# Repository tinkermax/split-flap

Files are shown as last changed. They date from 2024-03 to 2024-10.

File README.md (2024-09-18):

# Mechanical split-flap display
You can find full details and discussion on my [blog](https://tinkerwithtech.net/split-flap-display-brings-back-memories).

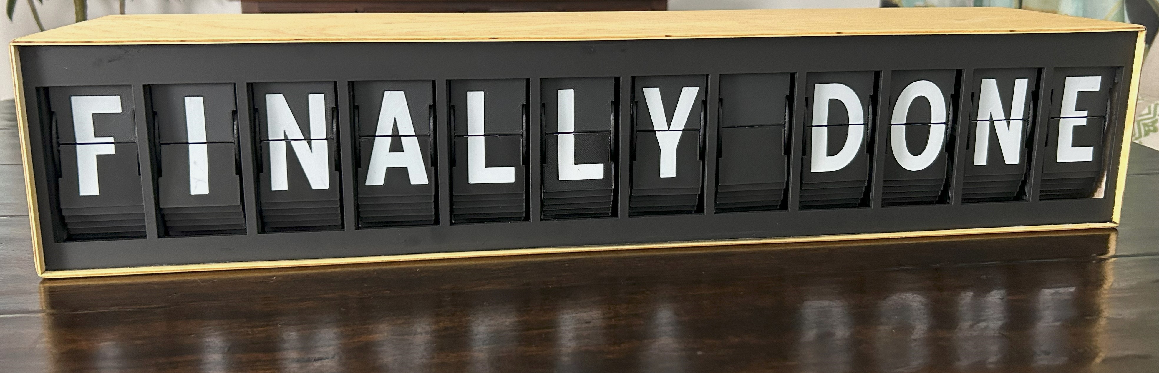
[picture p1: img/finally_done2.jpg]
Finished Split-Flap Project

<br/>

This is an alternate electronics and firmware for David Kingsman's [Split-Flap Display](https://www.printables.com/model/69464-split-flap-display).

### Advantages
* Only one microprocessor is needed to drive a 12 character display, instead of the 13 microprocessors that would be required in the original design.
* Off-the-shelf ribbon cables are used between PCBs to reduce custom wiring.
* All components are through-hole mounted (i.e. no SMD).
* Overall, this should reduce assembly time and effort.

### Disadvantages
* PCBs are not mounted to the back of the display units but have their own mounting brackets. This approach is best suited for use in your own enclosure.
* A display of greater than 12 characters would require an additional controller board i.e. may not be as seamless as the original.
<br/><br/>

## Settings
### Turn on interactions and debugging over the USB serial port in [debug.h](include/debug.h):
DEBUG 1
<br/>
### Specify the number of Units (characters) in your display (4 -12) in [system.h](include/system.h):
unitCount 12
### Specify the network name of the display (useful if you have more than one display) in [system.h](include/system.h):
NETWORKNAME "splitflap"
<br/>
### Customise for each unit for your build. (Units are numbered left to right 0 - 11) in [unit.h](include/unit.h):
calOffsetUnit : an array of the offsets to move from hall sensor trigger to blank flap<br/>
FlapStep : an array containing the number of steps per stepper revolution (then divided by 45 flaps)
<br/>
### Password and localisation settings in [config.h](include/config.h):
WIFI_SSID "mySSID"<br/>
WIFI_PWD "myPassword"

MY_NTP_SERVER "au.pool.ntp.org" // Set the best fitting NTP server (pool) for your location<br/>
MY_TZ "AEST-10AEDT,M10.1.0,M4.1.0/3" // Set your time zone from https://github.com/nayarsystems/posix_tz_db/blob/master/zones.csv

WORDNIKAPIKEY "" // Get your private key from https://developer.wordnik.com/<br/>
MINWORDLEN 9 // Specify minimum word length to fetch from Wordnik<br/>
WORDUPDATESPERHOUR 1 // Set number of word updates from https://wordnik.com per hour. 0 will disable, else use an integer that results in an exact number of minutes btw updates i.e. 1,2,3,4,5,6,10,12,15,20,30 or 60
<br/><br/>
## Libraries
This project makes extensive use of two libraries:
* [FastAccelStepper](https://github.com/gin66/FastAccelStepper) by J.Kiemes
* [arduino-mcp23017](https://github.com/blemasle/arduino-mcp23017) by Bertrand Lemasle
<br/><br/>

## Connecting to the display
### There is a very basic web page served at http://splitflap.local/ to allow you to either enter text to display or fetch a random word from Wordnik 

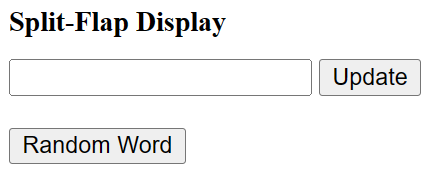
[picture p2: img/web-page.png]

<br/>

### There is also an API endpoint that you can POST to at http://splitflap.local/display, using a JSON payload in the body:

```json
{
    displaytext: "Display Text"
}
```

For example, you could use the request node within node-red:

<br/>
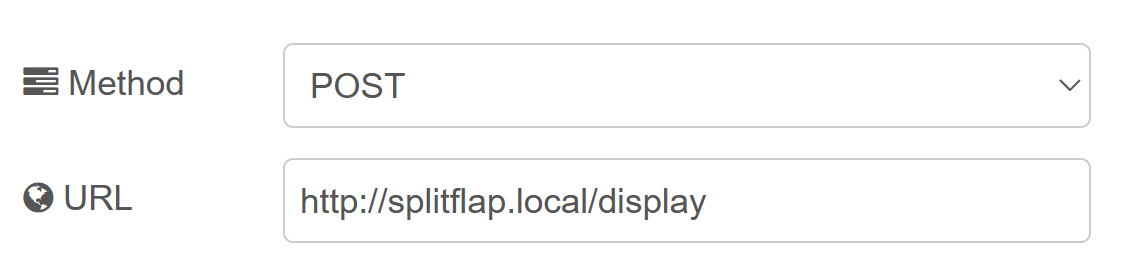
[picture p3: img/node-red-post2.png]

<br/><br/>

## PCBs
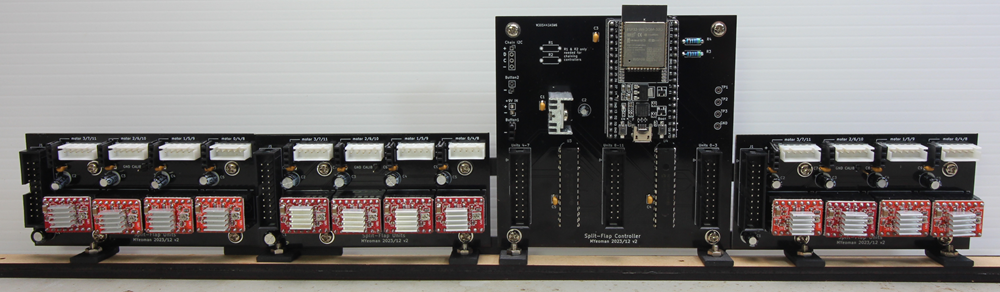
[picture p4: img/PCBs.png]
<br/>

Schematics for the Controller and Unit PCBs can be found under [schematics](schematics/).

Gerbers, Bill of materials and Kicad source files can be found under [PCBs](PCBs/).
<br/><br/>

## Brackets & unit frames 3D printing
PCB mounting brackets can be found on [Printables](https://www.printables.com/model/805853-split-flap-display).<br/> Also found there is my remixed unit frame. This is optional, as you could still use the original frames with the new electronics.
My unit frame requires an additional two M3\*L3\*D4 heat inserts for connecting to the adjacent unit.
<br/><br/>

## Enclosure (laser cut)

front<br/>
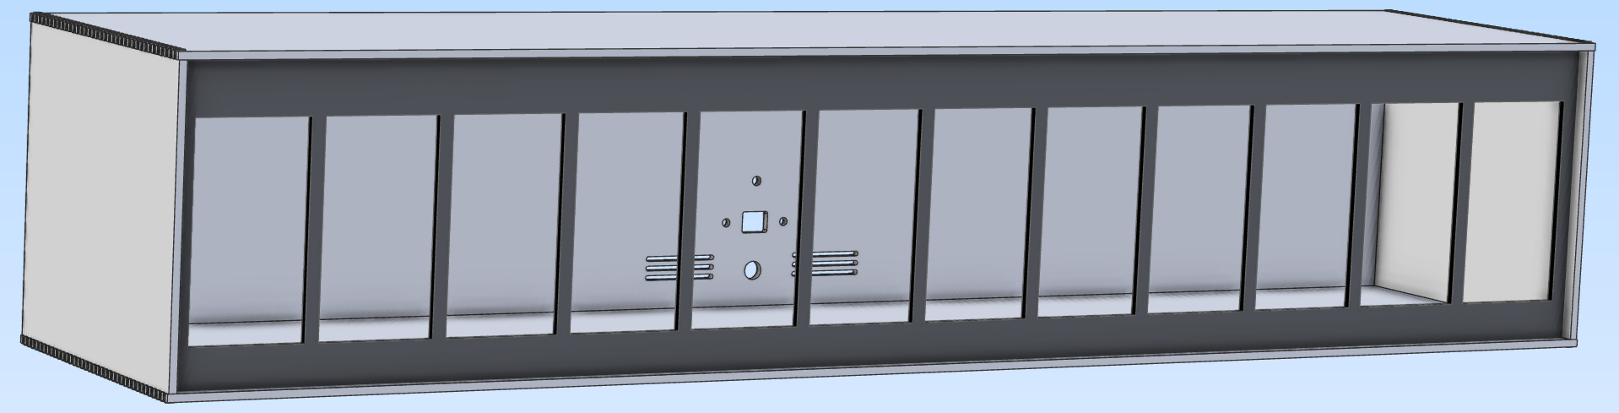
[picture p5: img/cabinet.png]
<br/>

rear<br/>
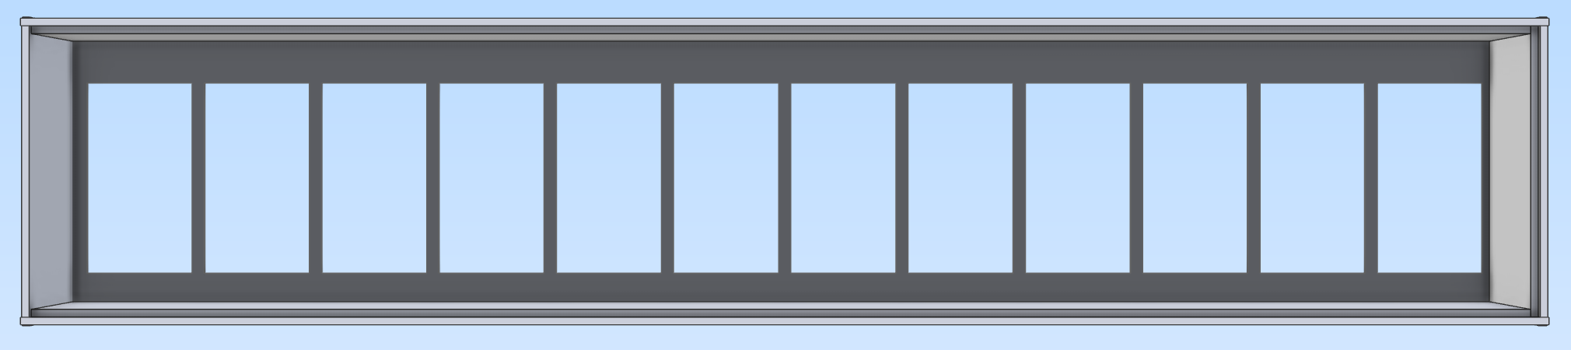
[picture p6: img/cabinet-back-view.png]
<br/>

Plywood (3mm) files for laser cutting are in [enclosure](enclosure/)
<br/><br/>

## Licensing
Copyright (c) 2024 Malcolm Yeoman.<br/>

Electronics is released under [CERN-OHL-P (Permissive) V2](https://ohwr.org/cern_ohl_p_v2.pdf).<br/>
Firmware is released under the [MIT License](http://opensource.org/licenses/MIT).<br/>
Documentation is licensed under a [Creative Commons Attribution 4.0 International License](http://creativecommons.org/licenses/by-sa/4.0/).

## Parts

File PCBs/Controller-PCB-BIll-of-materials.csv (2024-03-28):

Reference | Value | Footprint | Qty
C1,C3,C4,C5 | 100nF | Capacitor_THT:C_Disc_D3.4mm_W2.1mm_P2.50mm | 4
C2 | 10uF | Capacitor_THT:CP_Radial_D5.0mm_P2.00mm | 1
J1 | +9V IN | TerminalBlock_TE-Connectivity:TerminalBlock_TE_282834-3_1x03_P2.54mm_Horizontal | 1
J2 | Chain I2C | Connector_PinSocket_2.54mm:PinSocket_1x04_P2.54mm_Vertical | 1
J3 | Button1 | Connector_PinSocket_2.54mm:PinSocket_1x02_P2.54mm_Vertical | 1
J4 | Button2 | Connector_PinSocket_2.54mm:PinSocket_1x02_P2.54mm_Vertical | 1
J5 | Units 0-3 | Connector_IDC:IDC-Header_2x10_P2.54mm_Vertical | 1
J6 | Units 4-7 | Connector_IDC:IDC-Header_2x10_P2.54mm_Vertical | 1
J7 | Units 8-11 | Connector_IDC:IDC-Header_2x10_P2.54mm_Vertical | 1
R1,R2,R3,R4 | 4K7 | Resistor_THT:R_Axial_DIN0207_L6.3mm_D2.5mm_P7.62mm_Horizontal | 4
TP1,TP2,TP3,TP4 | 5000 | digikey-footprints:Test_Point_D1.02mm | 4
U1 | LD1117V33 | digikey-footprints:TO-220-3 | 1
U2 | ESP32-DevKitC | PCM_Espressif:ESP32-DevKitC | 1
U3,U4 | MCP23017 | digikey-footprints:DIP-28_W7.62mm | 2

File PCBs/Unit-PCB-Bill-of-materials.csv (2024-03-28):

Reference | Value | Datasheet | Footprint | Qty | DNP
A1,A2,A3,A4 | A4988 | https://www.pololu.com/product/2980/pictures | User:A4988_Stepper_Module | 4
C1,C2,C3,C4,C5 | 100uF | ~ | Capacitor_THT:CP_Radial_D6.3mm_P2.50mm | 5
C6,C7,C8,C9 | 100nF | ~ | Capacitor_THT:C_Disc_D3.4mm_W2.1mm_P2.50mm | 4
J1 | Units 0-3 | ~ | Connector_IDC:IDC-Header_2x10_P2.54mm_Vertical | 1
J2 | GND CALIB | ~ | Connector_PinHeader_2.54mm:PinHeader_1x01_P2.54mm_Vertical | 1
J3 | sens3 | ~ | Connector_PinSocket_2.54mm:PinSocket_1x03_P2.54mm_Vertical | 1
J4 | motor 3/7/11 | http://www.jst-mfg.com/product/pdf/eng/eXH.pdf | Connector_JST:JST_XH_B5B-XH-A_1x05_P2.50mm_Vertical | 1
J5 | sens2 | ~ | Connector_PinSocket_2.54mm:PinSocket_1x03_P2.54mm_Vertical | 1
J6 | motor 2/6/10 | http://www.jst-mfg.com/product/pdf/eng/eXH.pdf | Connector_JST:JST_XH_B5B-XH-A_1x05_P2.50mm_Vertical | 1
J7 | sens1 | ~ | Connector_PinSocket_2.54mm:PinSocket_1x03_P2.54mm_Vertical | 1
J8 | motor 1/5/9 | http://www.jst-mfg.com/product/pdf/eng/eXH.pdf | Connector_JST:JST_XH_B5B-XH-A_1x05_P2.50mm_Vertical | 1
J9 | sens0 | ~ | Connector_PinSocket_2.54mm:PinSocket_1x03_P2.54mm_Vertical | 1
J10 | motor 0/4/8 | http://www.jst-mfg.com/product/pdf/eng/eXH.pdf | Connector_JST:JST_XH_B5B-XH-A_1x05_P2.50mm_Vertical | 1

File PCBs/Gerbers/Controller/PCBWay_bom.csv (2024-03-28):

designator | quantity | value | pack | mpn | mount_type
C1, C3, C4, C5 | 4 | 100nF | C_Disc_D3.4mm_W2.1mm_P2.50mm |  | tht
C2 | 1 | 10uF | CP_Radial_D5.0mm_P2.00mm |  | tht
J1 | 1 | +9V IN | TerminalBlock_TE_282834-3_1x03_P2.54mm_Horizontal |  | tht
J2 | 1 | Chain I2C | PinSocket_1x04_P2.54mm_Vertical |  | tht
J3 | 1 | Button1 | PinSocket_1x02_P2.54mm_Vertical |  | tht
J4 | 1 | Button2 | PinSocket_1x02_P2.54mm_Vertical |  | tht
J5 | 1 | Units 0-3 | IDC-Header_2x10_P2.54mm_Vertical |  | tht
J6 | 1 | Units 4-7 | IDC-Header_2x10_P2.54mm_Vertical |  | tht
J7 | 1 | Units 8-11 | IDC-Header_2x10_P2.54mm_Vertical |  | tht
R1, R2, R3, R4 | 4 | 4K7 | R_Axial_DIN0207_L6.3mm_D2.5mm_P7.62mm_Horizontal |  | tht
REF1, REF2, REF3, REF4 | 4 | MountingHole_3.2mm_M3_Pad | MountingHole_3.2mm_M3_Pad |  | tht
TP1, TP2, TP3, TP4 | 4 | 5000 | Test_Point_D1.02mm | 5000 | tht
U1 | 1 | LD1117V33 | TO-220-3 | LD1117V33 | tht
U2 | 1 | ESP32-DevKitC | ESP32-DevKitC |  | tht
U3, U4 | 2 | MCP23017 | DIP-28_W7.62mm | MCP23017-E/SP | tht

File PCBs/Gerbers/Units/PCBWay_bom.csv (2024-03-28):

designator | quantity | value | pack | mpn | mount_type
A1, A2, A3, A4 | 4 | A4988 | A4988_Stepper_Module |  | tht
C1, C2, C3, C4, C5 | 5 | 100uF | CP_Radial_D6.3mm_P2.50mm |  | tht
C6, C7, C8, C9 | 4 | 100nF | C_Disc_D3.4mm_W2.1mm_P2.50mm |  | tht
J1 | 1 | Units 0-3 | IDC-Header_2x10_P2.54mm_Vertical |  | tht
J10 | 1 | motor 0/4/8 | JST_XH_B5B-XH-A_1x05_P2.50mm_Vertical | B5B-XH-A(LF)(SN) | tht
J2 | 1 | GND CALIB | PinHeader_1x01_P2.54mm_Vertical |  | tht
J3 | 1 | sens3 | PinSocket_1x03_P2.54mm_Vertical |  | tht
J4 | 1 | motor 3/7/11 | JST_XH_B5B-XH-A_1x05_P2.50mm_Vertical | B5B-XH-A(LF)(SN) | tht
J5 | 1 | sens2 | PinSocket_1x03_P2.54mm_Vertical |  | tht
J6 | 1 | motor 2/6/10 | JST_XH_B5B-XH-A_1x05_P2.50mm_Vertical | B5B-XH-A(LF)(SN) | tht
J7 | 1 | sens1 | PinSocket_1x03_P2.54mm_Vertical |  | tht
J8 | 1 | motor 1/5/9 | JST_XH_B5B-XH-A_1x05_P2.50mm_Vertical | B5B-XH-A(LF)(SN) | tht
J9 | 1 | sens0 | PinSocket_1x03_P2.54mm_Vertical |  | tht
REF1, REF2, REF3, REF4 | 4 | MountingHole_3.2mm_M3_Pad | MountingHole_3.2mm_M3_Pad |  | tht

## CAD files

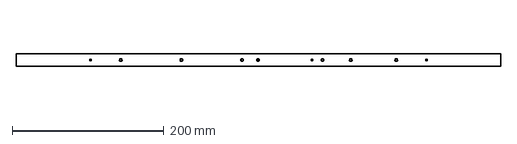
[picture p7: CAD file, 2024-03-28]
enclosure/PCB_Bracket-assembly-base.dxf
639.0 x 16.0 mm

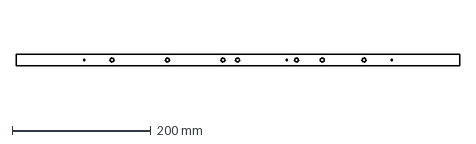
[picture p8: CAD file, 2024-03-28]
enclosure/PCB_Bracket-assembly-base2.dxf
639.0 x 16.0 mm

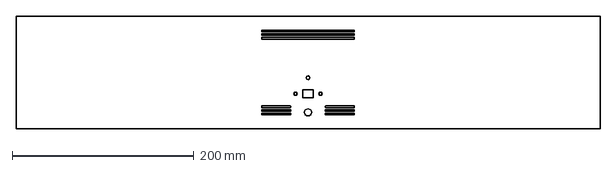
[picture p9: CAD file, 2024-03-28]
enclosure/back.dxf
642.5 x 123.5 mm

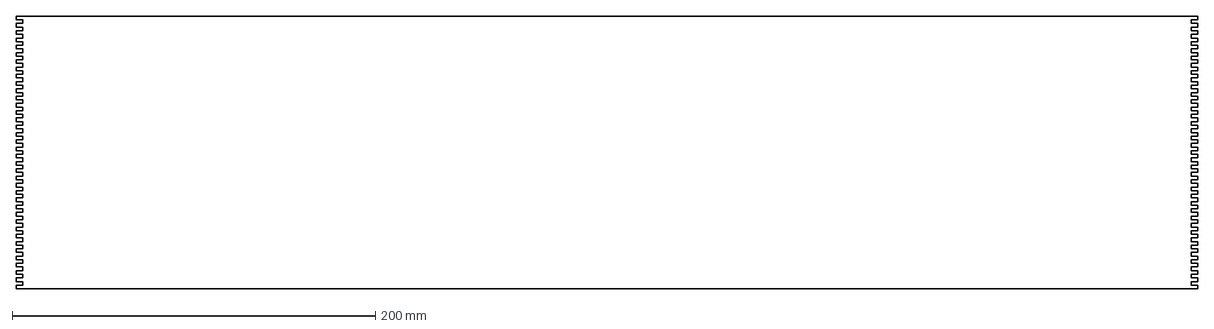
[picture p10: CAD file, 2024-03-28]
enclosure/top.dxf
650.4 x 150.0 mm

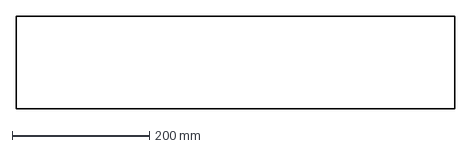
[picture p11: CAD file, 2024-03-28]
enclosure/shim_bottom.dxf
639.8 x 134.6 mm

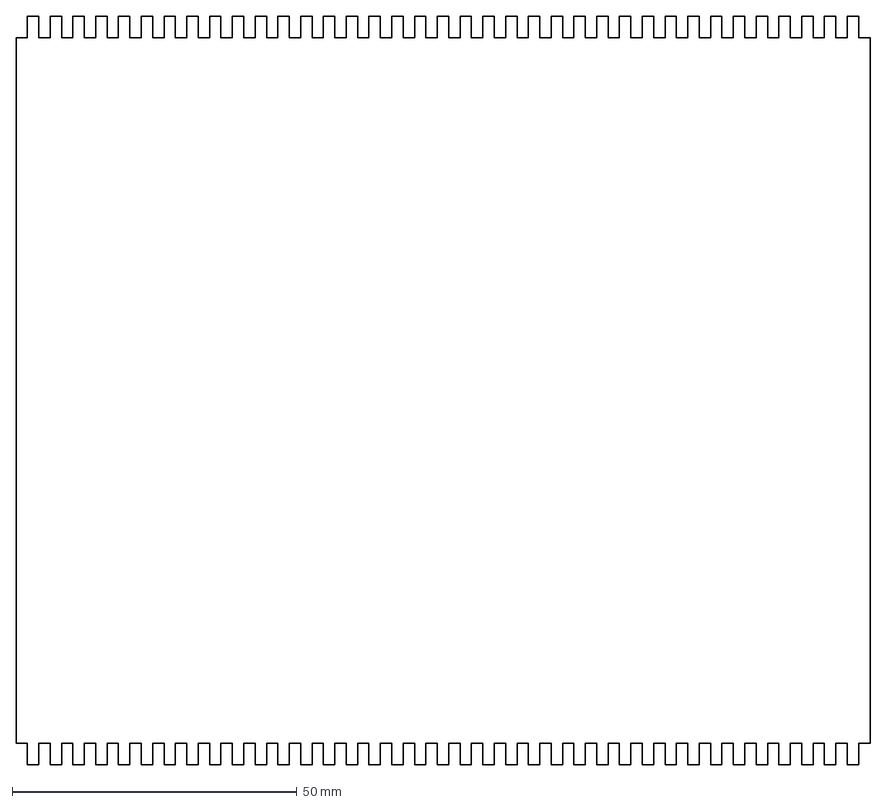
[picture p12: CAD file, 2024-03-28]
enclosure/side.dxf
150.0 x 131.4 mm

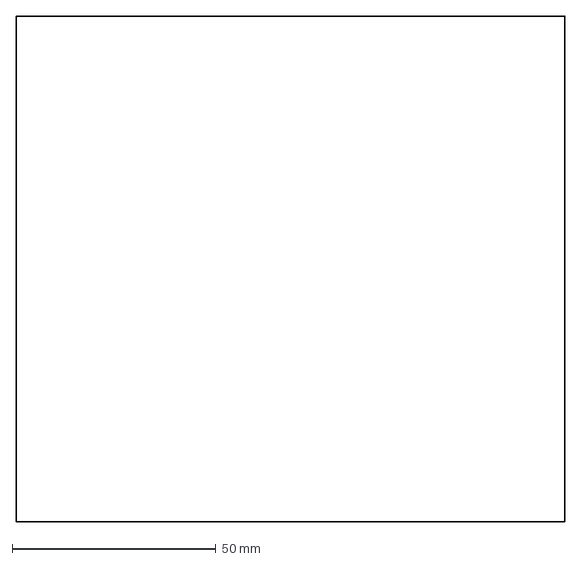
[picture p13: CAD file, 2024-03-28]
enclosure/shim.dxf
134.6 x 124.0 mm

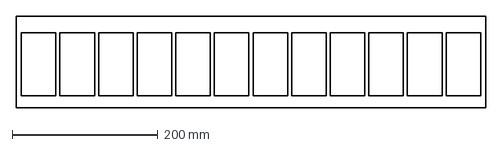
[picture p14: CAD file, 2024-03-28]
enclosure/panel.dxf
645.0 x 126.0 mm

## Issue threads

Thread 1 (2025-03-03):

Motor turning direction

Korny3005, 2025-03-03:
Hello,

im at building your system with 12 flaps and almost done.
I just struggle with some motor direction movements.
Most of them moving the wrong way. Only unit 11 is moving correct but this one does not home.

Any suggestion?

tinkermax, 2025-03-04:
I have 2 thoughts on the direction problem:
1. Have you made all the motors unipolar (by cutting the PCB track in each motor)?
2. Have you mounted the 4 sockets for the stepper motors the correct way - the open slots should face the outside of the PCB?

Not homing is a different issue related to the hall effect sensor. You could confirm that you are getting a low pulse on the sensor output when the drum magnet passes over (magnet needs to be orientated correctly).

tinkermax, 2025-03-04:
Interesting insight on swapping the orange and pink wires. Maybe there is a variation across manufacturers?
In the following 2 links, the motors have different colour sequences and (at least according to their wiring diagrams) it looks like the orientation of the coil wiring may be different.
[mine](https://ardufocus.com/howto/28byj-48-bipolar-hw-mod/)
[other](https://components101.com/motors/28byj-48-stepper-motor)
So you may be onto something!

Korny3005, 2025-03-04:
I think so too. I will open one Motor and check it out.
Im struggeling for hours and try and error.

EmEiBee, 2025-03-04:
... then I'll be a bit of a smartass ;)

NEVER rely on the color coding! Every manufacturer has their own idea; it might be right, but it doesn't have to be!

Basically, with undocumented stepper motors, use an ohmmeter to check which cable belongs to which coil package.

It's pretty easy with 4-pole motors. With 6-pole motors, you have to use an ohmmeter to determine the central connection (--- RL1a--|-- RL2a --- // --- RL1b--|-- RL2b ---), with 8-pole motors you can only apply current to one winding, add a second one and see whether the holding force has increased or decreased... It's really stupid if you don't have any documentation.

If a stepper motor is rotating the wrong way, you can either invert the signal on the driver or, as happened here, swap the external connections of ONE coil.

Of course, these considerations only apply to two-phase motors. Things get even more interesting with three-phase or multi-phase motors, but they are rarely used in the hobby sector.

Korny3005, 2025-03-04:
OMFG this could have saved me hours.
They just different Pins and colors…

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

EmEiBee, 2025-03-04:
Sorry I was too late to save you the trouble. But think positively: you certainly learned a lot from it...
Maybe I can still help with the Hall sensors? I don't know right now what was originally used and what you installed, but there are basically three different types of Hall sensors:
- Analog: Output voltage changes continuously with the magnetic field
- Digital Bipolar: These require a positive magnetic field to work and use the negative magnetic field to activate.
- Digital Unipolar: These only require a single magnetic south pole to work as they move in and out of the magnetic field.

Korny3005, 2025-03-04:
> Interesting insight on swapping the orange and pink wires. Maybe there is a variation across manufacturers? In the following 2 links, the motors have different colour sequences and (at least according to their wiring diagrams) it looks like the orientation of the coil wiring may be different. [mine](https://ardufocus.com/howto/28byj-48-bipolar-hw-mod/) [other](https://components101.com/motors/28byj-48-stepper-motor) So you may be onto something!

thank you for that variation hint. i will be more open minded next time.
I love your project. Thanks for answering here as well

tinkermax, 2025-03-04:
Thanks!

> source 5V from my ESP.

Just be aware that the ESP module will not _generate_ 5V from its 3.3V supply on the PCB (i.e. once you have disconnected the USB).

> the planned HALLs are not very common here in Europa

The big suppliers should have them e.g.
[Farnell](https://uk.farnell.com/allegro-microsystems/a1120lua-t/hall-effect-switch-unipolar-3sip/dp/1791404)
[Digikey](https://www.digikey.co.uk/en/products/detail/allegro-microsystems/A1120LUA-T/2075330)

EmEiBee, 2025-03-05:
> The big suppliers should have them e.g.

They only sell B2B and not to privat...

tinkermax, 2025-03-06:
> Another option would be TLE4905

Interesting... although according to the datasheet its minimum supply voltage is 3.8V so it wouldn't be a drop-in replacement.

tinkermax, 2025-03-06:
> They only sell B2B and not to private

Are you sure? I have previously bought from these companies without a problem. I just looked at the Farnell (UK) website and found this under their help section:

Do I have to be registered on the website to place an order?
You don't have to be registered on the website to place an order. You can checkout without registering.

Likewise, the forums are full of hobbyists who have ordered from Digikey (US). Only drawback may be the shipping costs.

Closed 2025-03-20.

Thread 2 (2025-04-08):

Not rotating

niels-hubs, 2025-04-08:
Hi TinkerMax!

Awesome project. We really played and struggled with it quite a bit. Now we are at the final stage.

We've build 12 units and made the PCB's for both the unit as the main controller PCB according to your instructions.
We've also cut the middle thing of the stepper motors according to the instructions (I think). We've also turned the screw so that the multimeter V HZ is showing 0.100 on the multimeter (or almost near 0.100 like 0.095, 0.092).

Now we are starting the 1.2 script, but it seems not to work. The stepper motors are making some kind of peeping sound almost constantly.
Also the script keeps restarting over and over. We've made sure that the boards are receiving the requested voltage.

We are really lost and could use your help debugging this issue.

`[  4185][E][Wire.cpp:513] requestFrom(): i2cRead returned Error 263
[  5192][E][Wire.cpp:513] requestFrom(): i2cRead returned Error 263
[  6199][E][Wire.cpp:513] requestFrom(): i2cRead returned Error 263
[  7207][E][Wire.cpp:513] requestFrom(): i2cRead returned Error 263
[  8214][E][Wire.cpp:513] requestFrom(): i2cRead returned Error 263
[  9221][E][Wire.cpp:513] requestFrom(): i2cRead returned Error 263
[ 10228][E][Wire.cpp:513] requestFrom(): i2cRead returned Error 263
[ 11235][E][Wire.cpp:513] requestFrom(): i2cRead returned Error 263
[ 12242][E][Wire.cpp:513] requestFrom(): i2cRead returned Error 263
[ 13249][E][Wire.cpp:513] requestFrom(): i2cRead returned Error 263
[ 14256][E][Wire.cpp:513] requestFrom(): i2cRead returned Error 263
Attempting to connect to SSID: Hubs

Connected to Hubs
192.168.50.168
[ 15285][E][Wire.cpp:513] requestFrom(): i2cRead returned Error 263
[ 16292][E][Wire.cpp:513] requestFrom(): i2cRead returned Error 263
[ 17299][E][Wire.cpp:513] requestFrom(): i2cRead returned Error 263
----------------------------------
     Tue Apr  8 22:53:15 2025
Enter a command followed by return
----------------------------------
\   : Show this menu
}   : Move ALL forward number of flaps
]   : Set active unit for this menu [0]
>   : Move forward number of flaps
~   : Move forward number steps
|   : Reset Display
%   : Display a random word
+   : Test: countdown of all flaps
<   : Idle
any : display given text
----------------------------------
Calibration started for Unit 0
Calibration started for Unit 1
Calibration started for Unit 2
Calibration started for Unit 3
Calibration started for Unit 4
Calibration started for Unit 5
Calibration started for Unit 6
Calibration started for Unit 7
Calibration started for Unit 8
Calibration started for Unit 9
Calibration started for Unit 10
Calibration started for Unit 11
[ 18545][E][Wire.cpp:513] requestFrom(): i2cRead returned Error 263
[ 19553][E][Wire.cpp:513] requestFrom(): i2cRead returned Error 263
Moving > 20 secs - RESTARTING!!!
ets Jul 29 2019 12:21:46

rst:0xc (SW_CPU_RESET),boot:0x13 (SPI_FAST_FLASH_BOOT)
configsip: 0, SPIWP:0xee
clk_drv:0x00,q_drv:0x00,d_drv:0x00,cs0_drv:0x00,hd_drv:0x00,wp_drv:0x00
mode:DIO, clock div:2
load:0x3fff0030,len:1184
load:0x40078000,len:13232
load:0x40080400,len:3028
entry 0x400805e4
Starting
[  1162][E][Wire.cpp:513] requestFrom(): i2cRead returned Error 263
[  2170][E][Wire.cpp:513] requestFrom(): i2cRead returned Error 263
[  3177][E][Wire.cpp:513] requestFrom(): i2cRead returned Error 263
[  4185][E][Wire.cpp:513] requestFrom(): i2cRead returned Error 263
[  5192][E][Wire.cpp:513] requestFrom(): i2cRead returned Error 263
[  6199][E][Wire.cpp:513] requestFrom(): i2cRead returned Error 263
[  7207][E][Wire.cpp:513] requestFrom(): i2cRead returned Error 263
[  8214][E][Wire.cpp:513] requestFrom(): i2cRead returned Error 263
[  9221][E][Wire.cpp:513] requestFrom(): i2cRead returned Error 263
[ 10228][E][Wire.cpp:513] requestFrom(): i2cRead returned Error 263
[ 11235][E][Wire.cpp:513] requestFrom(): i2cRead returned Error 263
[ 12242][E][Wire.cpp:513] requestFrom(): i2cRead returned Error 263
[ 13249][E][Wire.cpp:513] requestFrom(): i2cRead returned Error 263
[ 14256][E][Wire.cpp:513] requestFrom(): i2cRead returned Error 263
Attempting to connect to SSID: Hubs

Connected to Hubs
192.168.50.168
[ 15286][E][Wire.cpp:513] requestFrom(): i2cRead returned Error 263
[ 16293][E][Wire.cpp:513] requestFrom(): i2cRead returned Error 263
[ 17300][E][Wire.cpp:513] requestFrom(): i2cRead returned Error 263
previous_display: [], reboots: 0
----------------------------------
     Tue Apr  8 22:53:36 2025
Enter a command followed by return
----------------------------------
\   : Show this menu
}   : Move ALL forward number of flaps
]   : Set active unit for this menu [0]
>   : Move forward number of flaps
~   : Move forward number steps
|   : Reset Display
%   : Display a random word
+   : Test: countdown of all flaps
<   : Idle
any : display given text
----------------------------------
Calibration started for Unit 0
Calibration started for Unit 1
Calibration started for Unit 2
Calibration started for Unit 3
Calibration started for Unit 4
Calibration started for Unit 5
Calibration started for Unit 6
Calibration started for Unit 7
Calibration started for Unit 8
Calibration started for Unit 9
Calibration started for Unit 10
Calibration started for Unit 11
[ 18445][E][Wire.cpp:513] requestFrom(): i2cRead returned Error 263
[ 19453][E][Wire.cpp:513] requestFrom(): i2cRead returned Error 263
Guru Meditation Error: Core  0 panic'ed (Unhandled debug exception).
Debug exception reason: Stack canary watchpoint triggered (StepperTask)
Core  0 register dump:
PC      : 0x40090a85  PS      : 0x00060b36  A0      : 0x4008eeef  A1      : 0x3ffd0420
A2      : 0x3ffc6fb4  A3      : 0x3ffc6fc8  A4      : 0x3ffc6fc8  A5      : 0x00000001
A6      : 0x00000000  A7      : 0x00000018  A8      : 0x3ffc6fbc  A9      : 0x3ffd0400
A10     : 0x3ffd0bf0  A11     : 0x3ffd0bf0  A12     : 0x00000014  A13     : 0x00000000
A14     : 0x3ffd0be8  A15     : 0x80000001  SAR     : 0x00000004  EXCCAUSE: 0x00000001
EXCVADDR: 0x00000000  LBEG    : 0x4008b708  LEND    : 0x4008b71e  LCOUNT  : 0xffffffff

Backtrace: 0x40090a82:0x3ffd0420 0x4008eeec:0x3ffd0450 0x4008ee9c:0xa5a5a5a5 |<-CORRUPTED

ELF file SHA256: a9c070f3dcf6f34d

Rebooting...
ets Jul 29 2019 12:21:46
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
EmEiBee, 2025-04-08:
Maybe I'm able to help.
Pls let me see a picture of one of the modified stepper, similar to this one:

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

niels-hubs, 2025-04-08:
Thanks for the reply! I've made a picture of one of our stepper motors:

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

EmEiBee, 2025-04-08:
Ok, looks well so far. Have you measured the resistant between 2&5 to be sure that the connection is open?
I don't know the motors so I'm not sure between which contacts the coils are. I believe between 1&3 and the 2nd one between 4&6. If so, you can measure between 1&3 a low resistance, between 1&4 and 1&6 a high-z (open). May you like to check this. Disconnect the plug before.
Unfortunately, I can't open the schematics/PCBs uploaded here with my current version of KiCAD, for whatever reason.
Therefore, I have to assume that PIN 1 of the connectors points to the ribbon cable on t5he PCB? Is that correct?
If so, everything is connected correctly, if my assumption about the coils is correct.
The only thing that confuses me is the red wire on PIN 5 of the connector. Where does it lead?

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

niels-hubs, 2025-04-08:
I've measured the outputs, which all seems to be correct. I am currently testing with 1 set of full stepper motors (4 stepper motors). And only two of them are rotating. When I switch the ports (so I switch the ones that don't work around with the ones that do work, they start spinning but the other two that did work stop working).

I put the UNITCOUNT to 4 of course. I've also made a video of what is happening. https://streamable.com/1icrfd

EmEiBee, 2025-04-08:
hmmm...
So if I take your video and number it from left to right, the motors on ports 1 & 2 are running, but not on ports 3 & 4. Correct?
Have you also swap the stepper driver (1 with 3, 2 with 4) to be sure that all four driver are ok?
And have you turn the tiny trimmer of all driver to the same point, i.e. to middle?

niels-hubs, 2025-04-08:
Well, we made like 3 PCB's and we switched them around and we face the same problem on all PCB's. Also when we put the second motor on 0.100V it stops working, but the second stepper motor works when we put it on like 0.160v. Yet the other 2 (the latest) don't do anything. I read something on the blog about this, but I don't know if it is related:

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

EmEiBee, 2025-04-08:
I think that's not related to your problem. But it's ever a view in the glass ball, if you haven't the chance to take your own finger on the problem.
My approach now would be to use an oscilloscope to check the input signals of all four stages to see if they are receiving clean control signals. Then, if there are no anomalies, to compare the signals at the motor coils.
If that doesn't reveal any significant differences, I would place a driver PCB on a breadboard, connect a pulse generator (or an NE555 or NAND gates configured as a square-wave oscillator) and test every motor to see at what phase current each motor starts running.
But that requires a 2-channel scope and the knowledge of how to generate your square-wave pulses, or you would need to have a function generator.

If I were you, I'd proceed systematically and test each individual motor on the first port of the first PCB. If some motors aren't running, but others are, then the motors are probably the source of all the trouble.

If they're all running, then do the same with port 2 of the first PCB... and so on.

The driver PCBs don't care whether a motor is connected or not. So there's no need to populate all four ports with motors. Just one port at a time. And the other ports remain free...

tinkermax, 2025-04-08:
Hi niels-hubs

Thanks for providing so many details and photos.

> [ 15285][E][Wire.cpp:513] requestFrom(): i2cRead returned Error 263

This error indicates a fault with the i2c communications between the ESP32 and the MCP23017 chips, which (in theory) should be quite easy to troubleshoot.

You need to focus only on the main board. I suggest the following:
1. Maybe it's just the angle of the photo, but it doesn't look like there is much solder on the PCB joints for the ESP32 module? I would first add solder to all the ESP32 module pins to ensure connectivity to the PCB.
2. Check continuity from the ESP32 module pin marked "21" on the top of the module to pins 13 on both of the MCP23017 chips.
3. Check continuity from the ESP32 module pin marked "22" on the top of the module to pins 12 on both of the MCP23017 chips.

Beyond that, also measure to confirm you have 3.3V to the 3 chips i.e. pin 1 of the ESP32 module and both pins 9 of the MCP23017  chips.

Not related, but it looks like there might be a short on one of the unit boards (see the pic below). Again, may just be the angle.

Let me know how you go!

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

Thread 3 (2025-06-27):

Issue with small steps

HarshKumah, 2025-06-27:
Hello!

I am currently making this and have created 4 modules so far. It seems that when I set the Vref on the A4998 to 0.1V the motors don't want to turn, but at 0.16V they are. Is there a reason why this would be the case and am I damaging the motors.

Secondly, when I calibrate the module, I can get them to rotate 10 times and stay on the same character after 10 full rotations. But when I want to step them individually, for example 1 character at a time, they do not stay synced for a full rotation. For example I will move one flap but it will still be on the previous one.

Please let me know if you have any suggestions.

HarshKumah, 2025-06-28:
I am not very knowledgeable about coding so please understand. If the flap step is set to 1048.0/45, we get a 45.51 steps per flap. Does the motor/stepper driver deal with non-integer values?

tinkermax, 2025-06-28:
> after a few flaps...

Note that the ">" option is a basic low level test not intended for multiple sequential calls (since it does not make use of the recalibration sensor as the drum completes each revolution). A better test would be to just try the "display given text" to see if it rotates to the character you choose. If so, you're good to go.

> Did you have issues like this

No, but sticking sounds like a physical issue, maybe to do with the tolerances of the 3d printing. You could try boosting Vref as high as 0.2V to see if that helps.

> Does the motor/stepper driver deal with non-integer values?

If you look at the _stepsToRotate_ function, non-integer portions of a step are accumulated until they add up to a whole integer, after which they are applied. A single step is a very small movement - it is not necessary to go smaller.

HarshKumah, 2025-06-28:
That makes a lot of sense. Thanks, I think this has solved my issue. I adjust the stepsToRotate function and it works better now (and with Vref=0.2V)

Thank you for your quick responses. :)

Closed 2025-06-28.

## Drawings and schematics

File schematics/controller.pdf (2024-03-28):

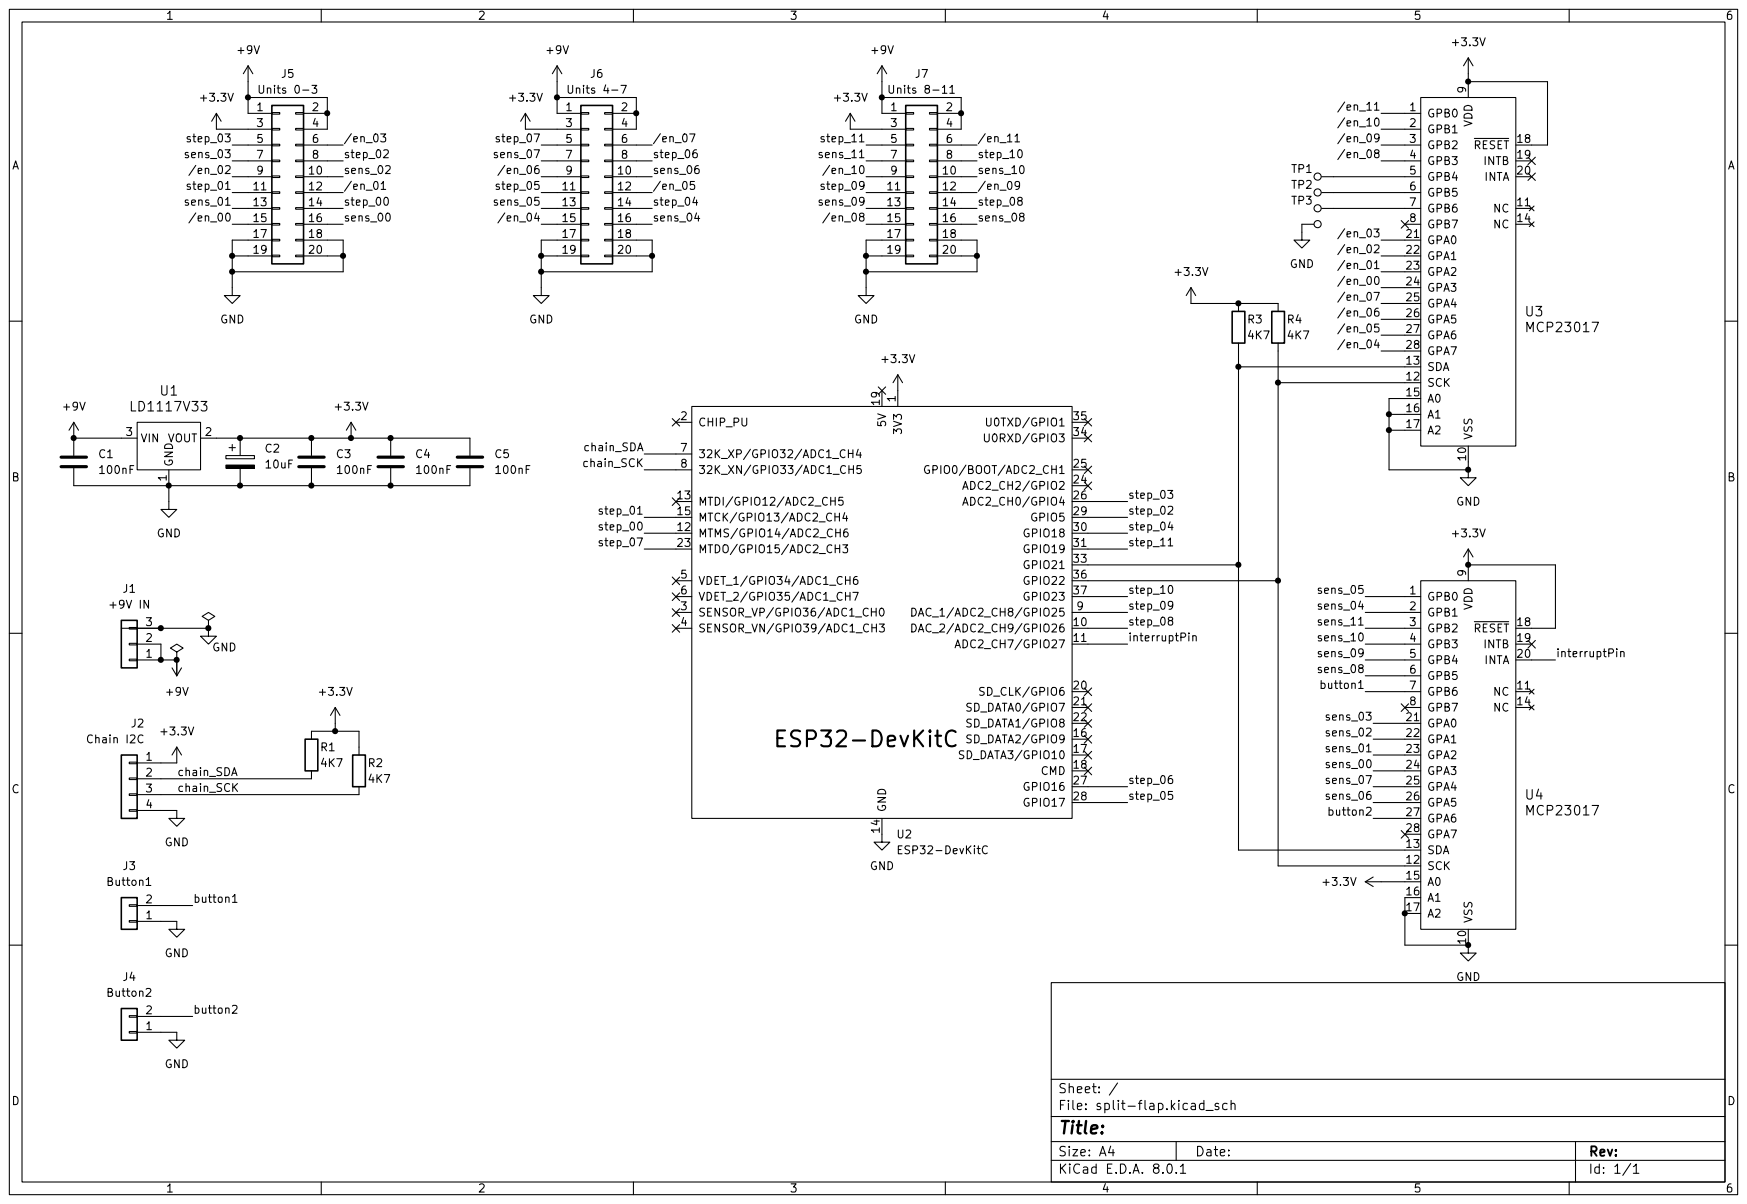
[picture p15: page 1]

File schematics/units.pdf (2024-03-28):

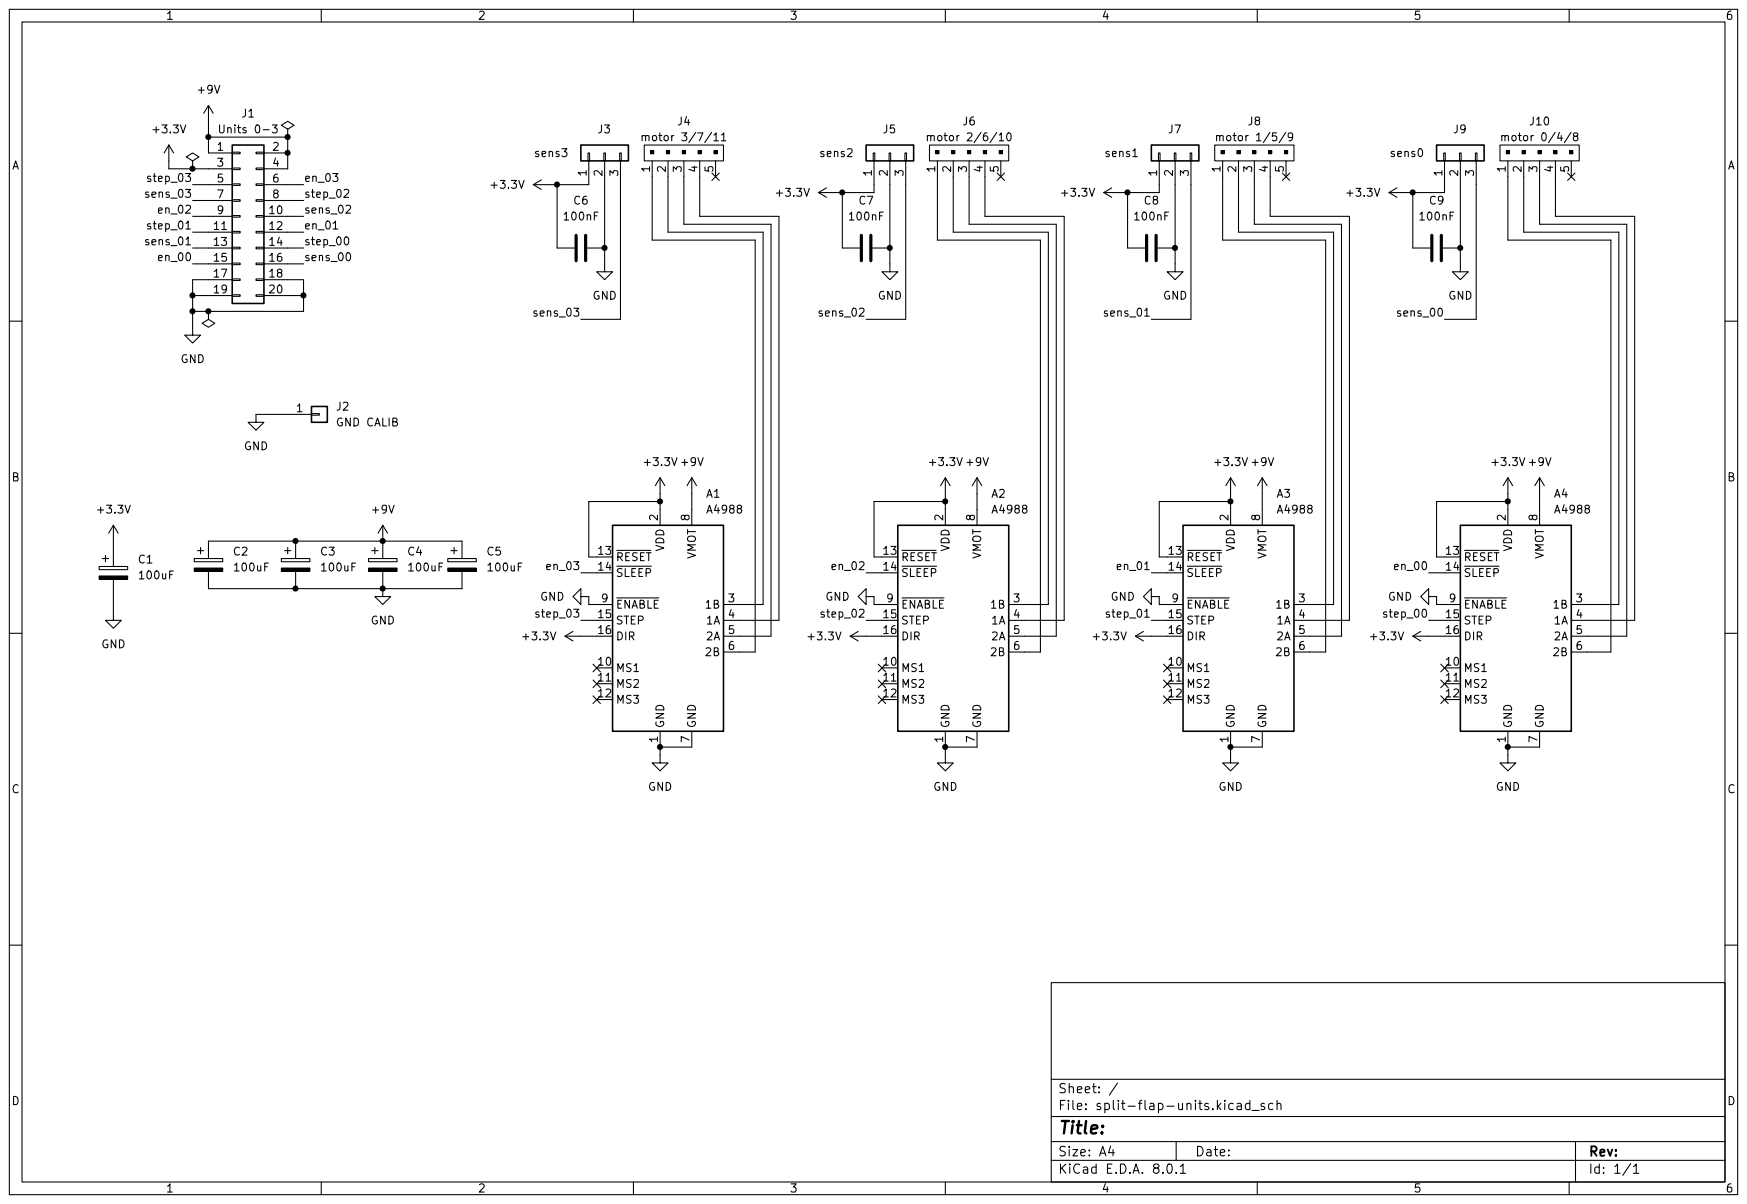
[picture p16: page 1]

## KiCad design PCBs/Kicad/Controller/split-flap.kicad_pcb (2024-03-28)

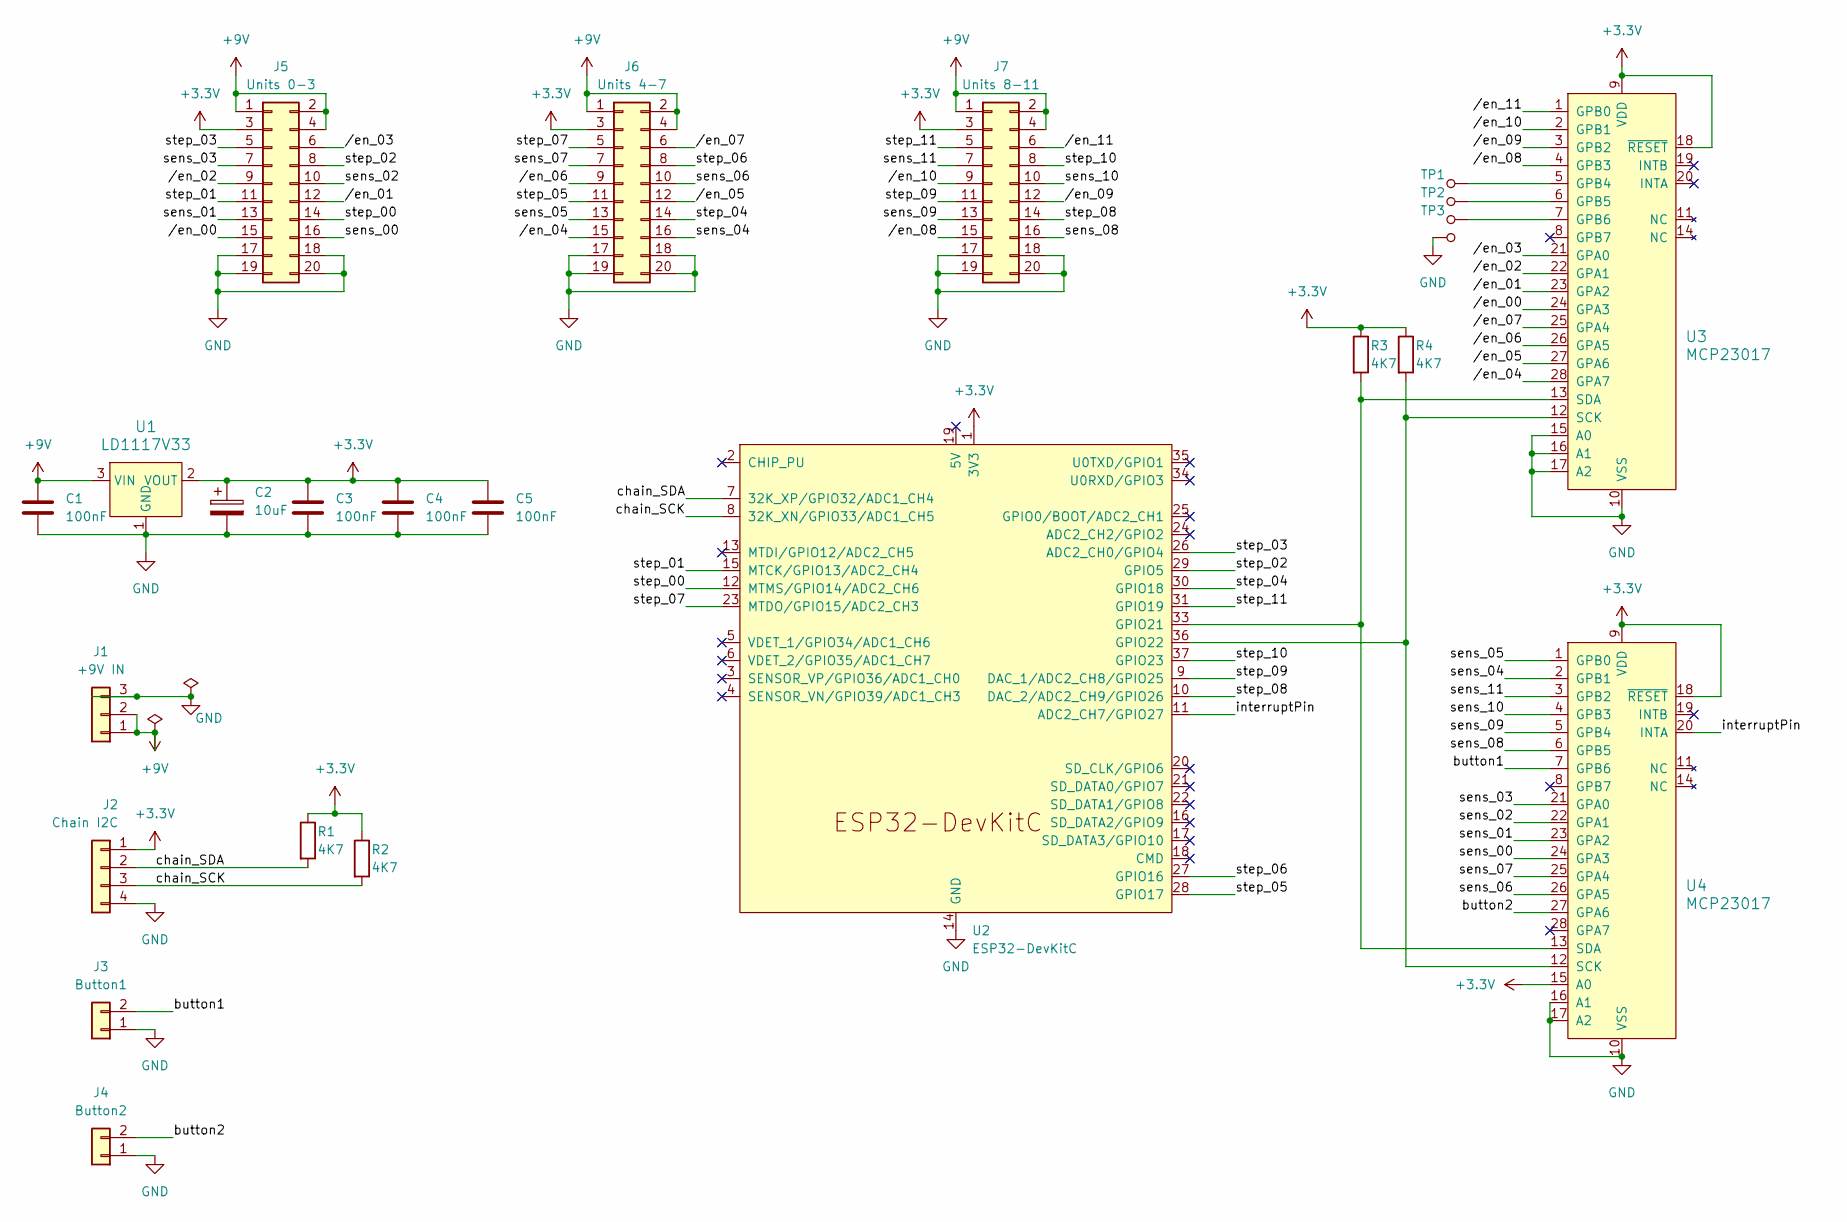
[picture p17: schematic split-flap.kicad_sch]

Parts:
C1, C3, C4, C5: 100nF; C_Disc_D3.4mm_W2.1mm_P2.50mm
C2: 10uF; CP_Radial_D5.0mm_P2.00mm
J1: +9V IN; TerminalBlock_TE_282834-3_1x03_P2.54mm_Horizontal
J2: Chain I2C; PinSocket_1x04_P2.54mm_Vertical
J3: Button1; PinSocket_1x02_P2.54mm_Vertical
J4: Button2; PinSocket_1x02_P2.54mm_Vertical
J5: Units 0-3; IDC-Header_2x10_P2.54mm_Vertical
J6: Units 4-7; IDC-Header_2x10_P2.54mm_Vertical
J7: Units 8-11; IDC-Header_2x10_P2.54mm_Vertical
R1, R2, R3, R4: 4K7; R_Axial_DIN0207_L6.3mm_D2.5mm_P7.62mm_Horizontal
TP1, TP2, TP3, TP4: 5000; Test_Point_D1.02mm; MPN 5000; Digi-Key_PN 36-5000-ND
U1: LD1117V33; TO-220-3; MPN LD1117V33; Digi-Key_PN 497-1491-5-ND
U2: ESP32-DevKitC
U3, U4: MCP23017; DIP-28_W7.62mm; MPN MCP23017-E/SP; Digi-Key_PN MCP23017-E/SP-ND

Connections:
+3.3V: C2.1, C3.1, C4.1, C5.1, J2.1, J5.3, J6.3, J7.3, R1.1, R2.1, R3.1, R4.1, U1.2 (VOUT), U2.1 (3V3), U3.9 (VDD), U3.18 (~RESET), U4.9 (VDD), U4.15 (A0), U4.18 (~RESET)
+9V: C1.1, J1.1, J1.2, J5.1, J5.2, J5.4, J6.1, J6.2, J6.4, J7.1, J7.2, J7.4, U1.3 (VIN)
/button1: J3.2, U4.7 (GPB6)
/button2: J4.2, U4.27 (GPA6)
/chain_SCK: J2.3, R2.2, U2.8 (32K_XN/GPIO33/ADC1_CH5)
/chain_SDA: J2.2, R1.2, U2.7 (32K_XP/GPIO32/ADC1_CH4)
/interruptPin: U2.11 (ADC2_CH7/GPIO27), U4.20 (INTA)
/sens_00: J5.16, U4.24 (GPA3)
/sens_01: J5.13, U4.23 (GPA2)
/sens_02: J5.10, U4.22 (GPA1)
/sens_03: J5.7, U4.21 (GPA0)
/sens_04: J6.16, U4.2 (GPB1)
/sens_05: J6.13, U4.1 (GPB0)
/sens_06: J6.10, U4.26 (GPA5)
/sens_07: J6.7, U4.25 (GPA4)
/sens_08: J7.16, U4.6 (GPB5)
/sens_09: J7.13, U4.5 (GPB4)
/sens_10: J7.10, U4.4 (GPB3)
/sens_11: J7.7, U4.3 (GPB2)
/step_00: J5.14, U2.12 (MTMS/GPIO14/ADC2_CH6)
/step_01: J5.11, U2.15 (MTCK/GPIO13/ADC2_CH4)
/step_02: J5.8, U2.29 (GPIO5)
/step_03: J5.5, U2.26 (ADC2_CH0/GPIO4)
/step_04: J6.14, U2.30 (GPIO18)
/step_05: J6.11, U2.28 (GPIO17)
/step_06: J6.8, U2.27 (GPIO16)
/step_07: J6.5, U2.23 (MTDO/GPIO15/ADC2_CH3)
/step_08: J7.14, U2.10 (DAC_2/ADC2_CH9/GPIO26)
/step_09: J7.11, U2.9 (DAC_1/ADC2_CH8/GPIO25)
/step_10: J7.8, U2.37 (GPIO23)
/step_11: J7.5, U2.31 (GPIO19)
//en_00: J5.15, U3.24 (GPA3)
//en_01: J5.12, U3.23 (GPA2)
//en_02: J5.9, U3.22 (GPA1)
//en_03: J5.6, U3.21 (GPA0)
//en_04: J6.15, U3.28 (GPA7)
//en_05: J6.12, U3.27 (GPA6)
//en_06: J6.9, U3.26 (GPA5)
//en_07: J6.6, U3.25 (GPA4)
//en_08: J7.15, U3.4 (GPB3)
//en_09: J7.12, U3.3 (GPB2)
//en_10: J7.9, U3.2 (GPB1)
//en_11: J7.6, U3.1 (GPB0)
GND: C1.2, C2.2, C3.2, C4.2, C5.2, J1.3, J2.4, J3.1, J4.1, J5.17, J5.18, J5.19, J5.20, J6.17, J6.18, J6.19, J6.20, J7.17, J7.18, J7.19, J7.20, TP4.1, U1.1 (GND), U2.14 (GND), U2.32 (GND), U2.38 (GND), U3.10 (VSS), U3.15 (A0), U3.16 (A1), U3.17 (A2), U4.10 (VSS), U4.16 (A1), U4.17 (A2)
unnamed: R3.2, U2.33 (GPIO21), U3.13 (SDA), U4.13 (SDA)
unnamed: R4.2, U2.36 (GPIO22), U3.12 (SCK), U4.12 (SCK)
unnamed: TP1.1, U3.5 (GPB4)
unnamed: TP2.1, U3.6 (GPB5)
unnamed: TP3.1, U3.7 (GPB6)

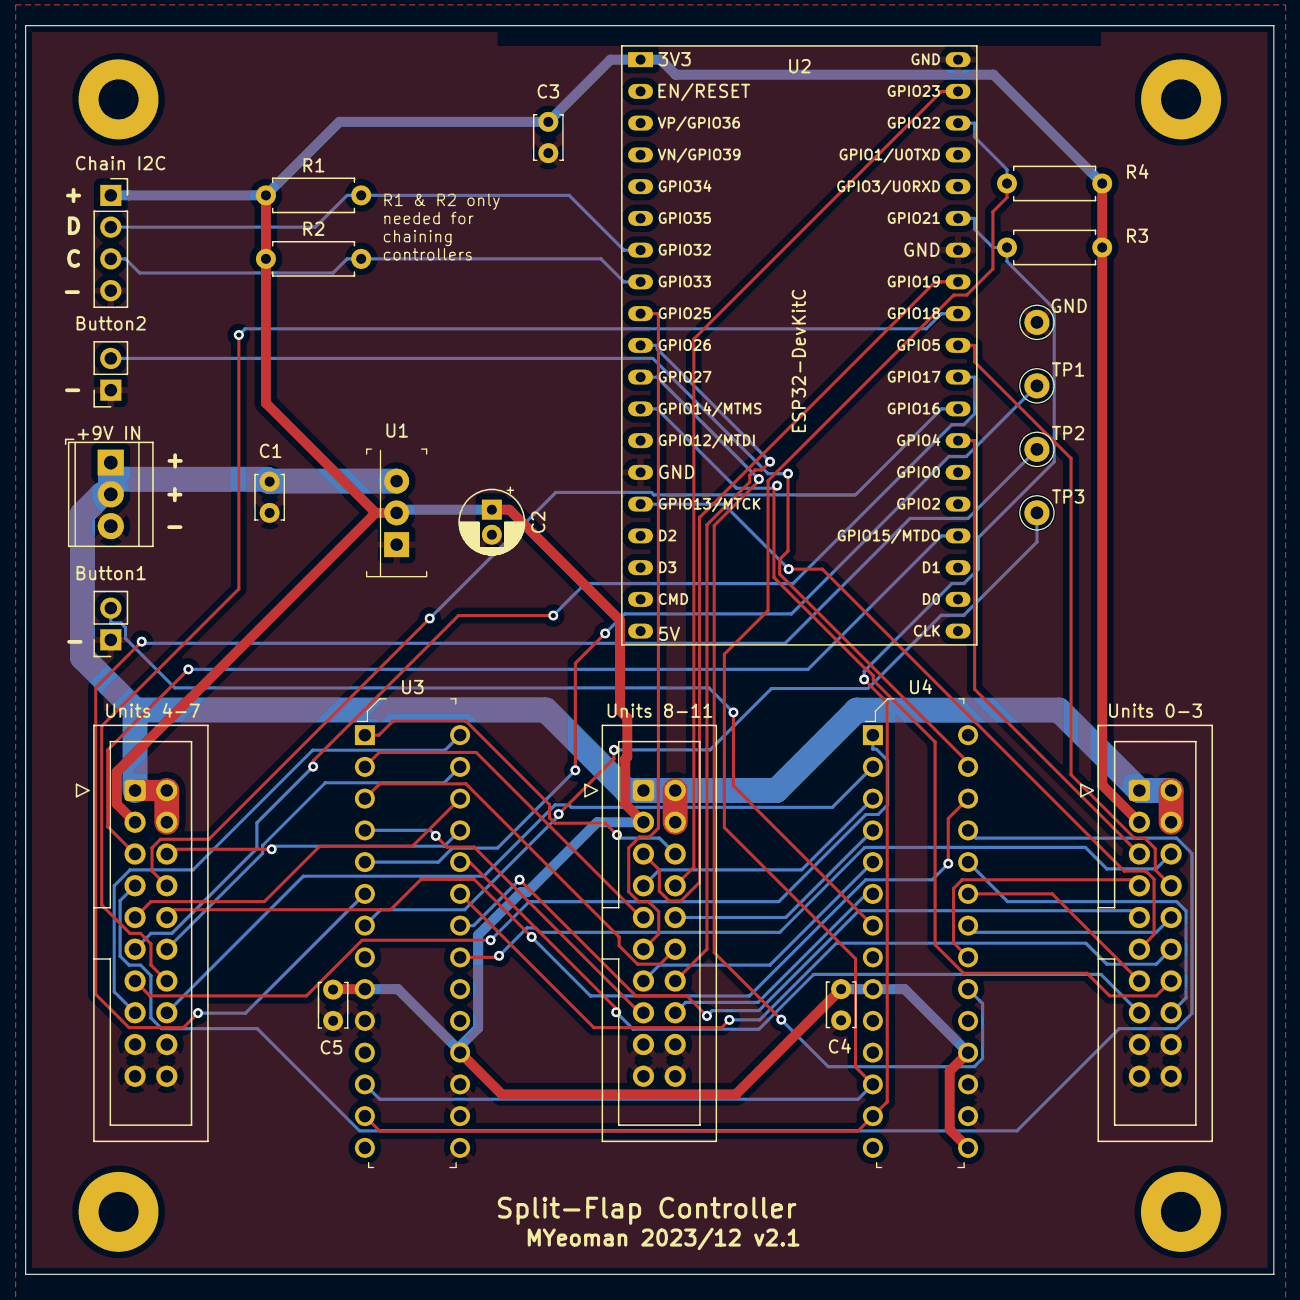
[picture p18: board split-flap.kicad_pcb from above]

Board: 2 copper layers, 99.9 x 99.9 mm, 28 parts (0 on the bottom side), 49 nets.

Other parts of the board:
REF1, REF2, REF3, REF4: MountingHole_3.2mm_M3_Pad

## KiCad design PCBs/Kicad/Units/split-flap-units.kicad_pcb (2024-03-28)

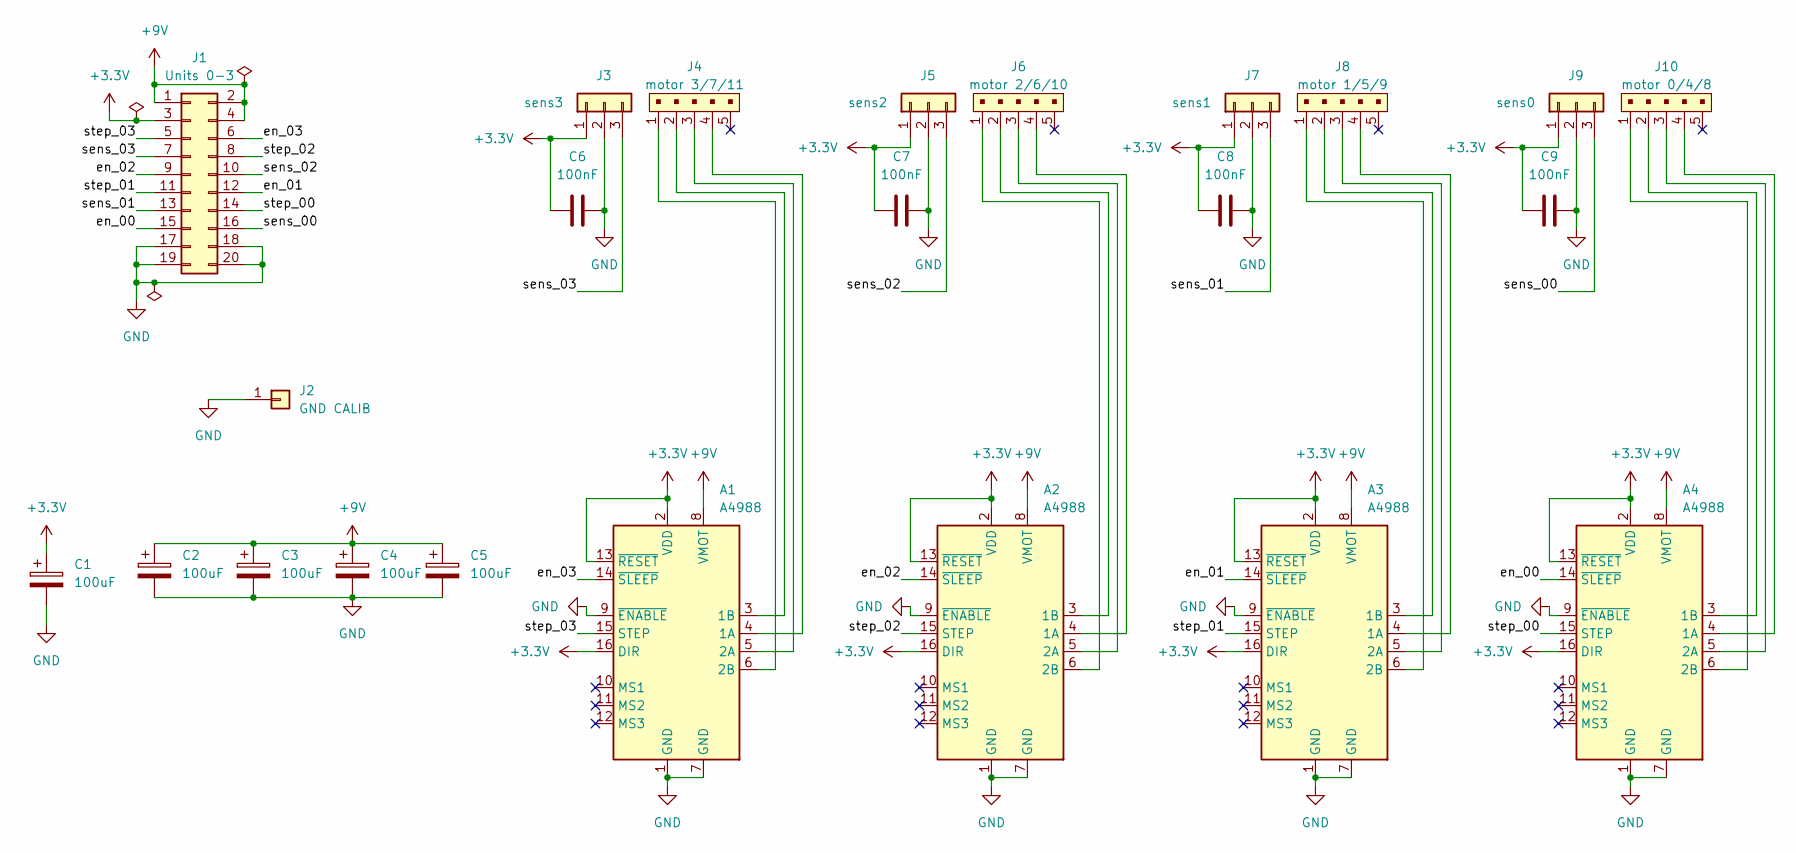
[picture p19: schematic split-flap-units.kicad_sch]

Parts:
A1, A2, A3, A4: A4988; A4988_Stepper_Module
C1, C2, C3, C4, C5: 100uF; CP_Radial_D6.3mm_P2.50mm
C6, C7, C8, C9: 100nF; C_Disc_D3.4mm_W2.1mm_P2.50mm
J1: Units 0-3; IDC-Header_2x10_P2.54mm_Vertical
J2: GND CALIB; PinHeader_1x01_P2.54mm_Vertical
J3: sens3; PinSocket_1x03_P2.54mm_Vertical
J4: motor 3/7/11; JST_XH_B5B-XH-A_1x05_P2.50mm_Vertical; MPN B5B-XH-A(LF)(SN); Digi-Key_PN 455-2270-ND
J5: sens2; PinSocket_1x03_P2.54mm_Vertical
J6: motor 2/6/10; JST_XH_B5B-XH-A_1x05_P2.50mm_Vertical; MPN B5B-XH-A(LF)(SN); Digi-Key_PN 455-2270-ND
J7: sens1; PinSocket_1x03_P2.54mm_Vertical
J8: motor 1/5/9; JST_XH_B5B-XH-A_1x05_P2.50mm_Vertical; MPN B5B-XH-A(LF)(SN); Digi-Key_PN 455-2270-ND
J9: sens0; PinSocket_1x03_P2.54mm_Vertical
J10: motor 0/4/8; JST_XH_B5B-XH-A_1x05_P2.50mm_Vertical; MPN B5B-XH-A(LF)(SN); Digi-Key_PN 455-2270-ND

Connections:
+3.3V: A1.2 (VDD), A1.13 (~RESET), A1.16 (DIR), A2.2 (VDD), A2.13 (~RESET), A2.16 (DIR), A3.2 (VDD), A3.13 (~RESET), A3.16 (DIR), A4.2 (VDD), A4.13 (~RESET), A4.16 (DIR), C1.1, C6.1, C7.1, C8.1, C9.1, J1.3, J3.1, J5.1, J7.1, J9.1
+9V: A1.8 (VMOT), A2.8 (VMOT), A3.8 (VMOT), A4.8 (VMOT), C2.1, C3.1, C4.1, C5.1, J1.1, J1.2, J1.4
/en_00: A4.14 (~SLEEP), J1.15
/en_01: A3.14 (~SLEEP), J1.12
/en_02: A2.14 (~SLEEP), J1.9
/en_03: A1.14 (~SLEEP), J1.6
/sens_00: J1.16, J9.3
/sens_01: J1.13, J7.3
/sens_02: J1.10, J5.3
/sens_03: J1.7, J3.3
/step_00: A4.15 (STEP), J1.14
/step_01: A3.15 (STEP), J1.11
/step_02: A2.15 (STEP), J1.8
/step_03: A1.15 (STEP), J1.5
GND: A1.1 (GND), A1.7 (GND), A1.9 (~ENABLE), A2.1 (GND), A2.7 (GND), A2.9 (~ENABLE), A3.1 (GND), A3.7 (GND), A3.9 (~ENABLE), A4.1 (GND), A4.7 (GND), A4.9 (~ENABLE), C1.2, C2.2, C3.2, C4.2, C5.2, C6.2, C7.2, C8.2, C9.2, J1.17, J1.18, J1.19, J1.20, J2.1, J3.2, J5.2, J7.2, J9.2
unnamed: A1.4 (1A), J4.4
unnamed: A1.3 (1B), J4.2
unnamed: A1.5 (2A), J4.3
unnamed: A1.6 (2B), J4.1
unnamed: A2.4 (1A), J6.4
unnamed: A2.3 (1B), J6.2
unnamed: A2.5 (2A), J6.3
unnamed: A2.6 (2B), J6.1
unnamed: A3.4 (1A), J8.4
unnamed: A3.3 (1B), J8.2
unnamed: A3.5 (2A), J8.3
unnamed: A3.6 (2B), J8.1
unnamed: A4.4 (1A), J10.4
unnamed: A4.3 (1B), J10.2
unnamed: A4.5 (2A), J10.3
unnamed: A4.6 (2B), J10.1

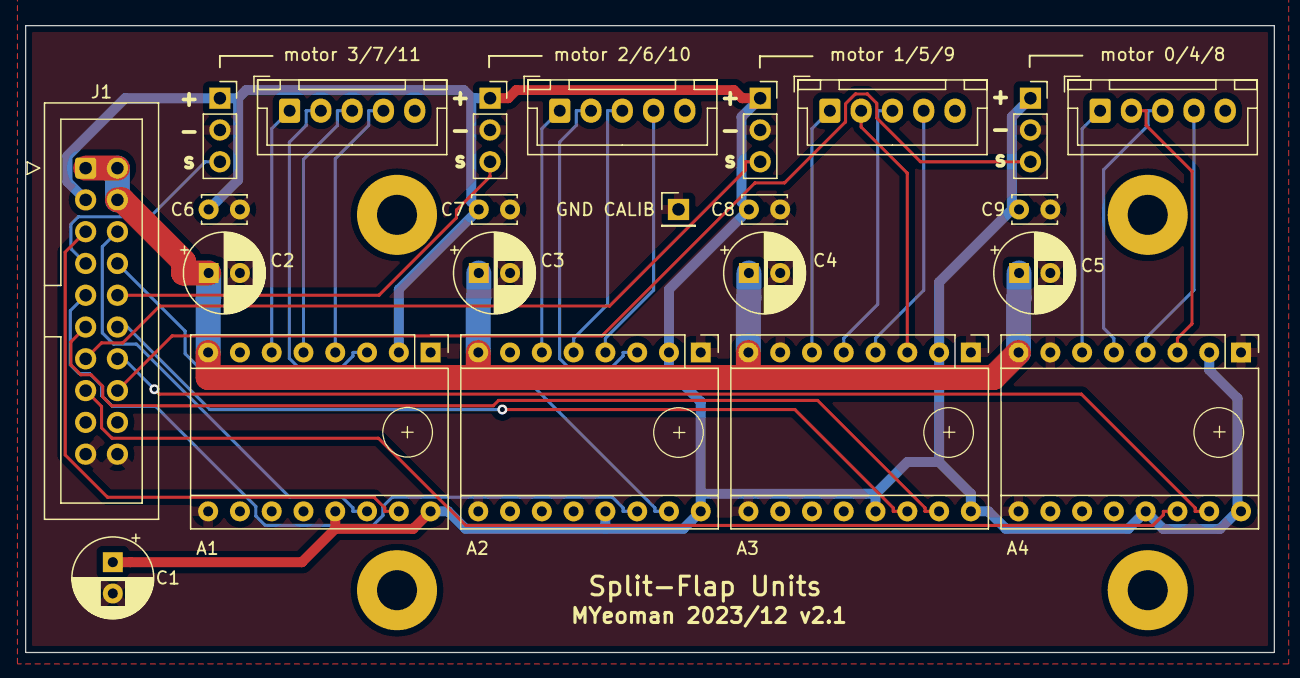
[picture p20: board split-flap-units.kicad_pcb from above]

Board: 2 copper layers, 99.8 x 50.1 mm, 27 parts (0 on the bottom side), 31 nets.

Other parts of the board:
REF1, REF2, REF3, REF4: MountingHole_3.2mm_M3_Pad

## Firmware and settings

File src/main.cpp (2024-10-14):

/* Firmware for Mechanical Split-Flap Display
 *
 * This is the Arduino firmware for esp32Core_board_v2 (ESP32 DevKitC)
 *
 * Malcolm Yeoman (2024)
 *
 * Blog post: https://tinkerwithtech.net/split-flap-display-brings-back-memories
 * Github:
 *
 * Note1: Implemented so that on the MCP23017 GPA7 and GPB7 are not used as inputs
 *        https://microchipsupport.force.com/s/article/GPA7---GPB7-Cannot-Be-Used-as-Inputs-In-MCP23017
 *
*/

#include <Arduino.h>
#include <Wire.h>
#include <MCP23017.h>
#include <time.h>
#include "system.h"
#include "unit.h"
#if __has_include(<config-private.h>)
    #include "config-private.h"
#else
    #include "config.h"
#endif

// Function headers
void print_test_menu ();
bool setExternalPin(uint8_t pin, uint8_t value);
// boolean calibrate_all_units();
void recalibrate_units();
void IRAM_ATTR sensor_ISR();
void updateHallSensors();
void displayString(String display);
boolean diplayStillMoving();
// void intToBinary(int num, char* binaryStr);
// void debugUnitFlags(String prefix);

// Global vars
uint32_t previousMillis = 0;
uint32_t displayLastStoppedMillis;
uint32_t nextWordAPIMillis = 0;
MCP23017 mcp_en_steppers = MCP23017(0x20);
MCP23017 mcp_sensor = MCP23017(0x21);
Unit *splitFlap[UNITCOUNT];
volatile bool sensortriggered = false;
uint16_t counter = 0;
uint8_t active_menu_unit = 0;
boolean getting_first_word = true;
const char* ssid = WIFI_SSID;
const char* password = WIFI_PWD;
time_t now; // this is the epoch
tm timeinfo;  // structure tm holds time information in a more convenient way
String test_command_previous = "";
uint8_t charSeq = 40;
char save_display[13];
char previous_display[13];
uint8_t reboot_count;
String localIP;
FastAccelStepperEngine engine;
extern WebServer server;
uint8_t word_updates_per_hour = WORDUPDATESPERHOUR; //store config value in variable to prevent div by zero compiler warnings

// RTC memory structure - for persisting data between reboots
typedef struct {
  uint32_t magic;
  char previous_display[13];
  uint8_t reboot_count;
} RTC;
RTC_NOINIT_ATTR RTC nvmem;


// SETUP
void setup() {

#if DEBUG == 1
  Serial.begin(115200);
#endif
  
  WiFi.begin(ssid, password);
  debugln(TXT_BLUE "Starting" TXT_RST);

  // Future expansion possibility: Set up external I2C to chain multiple controller boards
  // Wire2.begin(32,33); //(SDA=32, SCL=33);

  // Configure I2C for MCP23017 port expanders
  Wire.begin(21, 22, 800000); // SDA=21, SCL=22, 800kHz

  mcp_en_steppers.init();
  mcp_en_steppers.portMode(MCP23017Port::A, 0);          //Port A as output
  mcp_en_steppers.portMode(MCP23017Port::B, 0);          //Port B as output
  mcp_en_steppers.writeRegister(MCP23017Register::GPIO_A, 0x00);  //Reset port A 
  mcp_en_steppers.writeRegister(MCP23017Register::GPIO_B, 0x00);  //Reset port B

  mcp_sensor.init();
  mcp_sensor.portMode(MCP23017Port::A, 0b01111111); //Port A 7 bits as input
  mcp_sensor.portMode(MCP23017Port::B, 0b01111111); //Port B 7 bits as input
  mcp_sensor.writeRegister(MCP23017Register::IPOL_A, 0x00);
  mcp_sensor.writeRegister(MCP23017Register::IPOL_B, 0x00);
  mcp_sensor.writeRegister(MCP23017Register::GPIO_A, 0xFF);
  mcp_sensor.writeRegister(MCP23017Register::GPIO_B, 0xFF);

  // Set up fast stepper engine
  engine = FastAccelStepperEngine();
  engine.init();
  engine.setExternalCallForPin(setExternalPin);

  // Initialise split-flap display units
  for (uint8_t unit = 0; unit < UNITCOUNT; unit++) {
    splitFlap[unit] = new Unit(engine, unit);
  }

  // Enable Sensor interrupts
  mcp_sensor.interruptMode(MCP23017InterruptMode::Or); //Both ports logically ORed to same interrupt pin     
  mcp_sensor.interrupt(MCP23017Port::A, CHANGE);
  mcp_sensor.interrupt(MCP23017Port::B, CHANGE);
  mcp_sensor.clearInterrupts();
  pinMode(interruptPin, INPUT_PULLUP);
  attachInterrupt(digitalPinToInterrupt(interruptPin), sensor_ISR, FALLING);

  // attempt to connect to Wifi network
  debug("Attempting to connect to SSID: ");
  debugln(ssid);
  while (WiFi.status() != WL_CONNECTED) {
    debug(".");
    // wait 1 second between retries
    delay(1000);
  }

  debug("\nConnected to " TXT_BLUE);
  debugln(ssid);
  localIP = WiFi.localIP().toString();
  debug(localIP);
  debugln(TXT_RST);

  disableCertificates(); 

  // Lookup NTP time
  configTzTime(MY_TZ, MY_NTP_SERVER);
  now = time(nullptr); //start time sync in background

  // Set up REST API
  setup_routing();

  // Read hall sensors to get current values
  updateHallSensors();

  // Read any previous display before last reboot
  if (nvmem.magic == RTC_MAGIC) {
    strncpy(previous_display, nvmem.previous_display, 13);
    previous_display[12]='\0';
    reboot_count = nvmem.reboot_count;
    debugf(TXT_YELLOW "previous_display: [%s], reboots: %d\n" TXT_RST, previous_display, reboot_count);
  }
  else {
    previous_display[0] = '\0';
    reboot_count = 0;
  }

  delay(101); // Delay to avoid initially false triggering the glitch detection

  // Try up to 3 times to get NTP
  uint8_t getntpcount = 0;
  while (getntpcount++ < 3 && !getNTP(now, timeinfo)) {
    delay(1000);
    debugln("Retrying NTP...");
  }

  displayLastStoppedMillis = 0;

#if DEBUG == 1
  print_test_menu();
#endif
}

void loop() {
  String test_command;
  uint16_t test_num;

  ////////////////////////
  // HIGH LEVEL EVENT LOOP
  ////////////////////////

  // Read hall sensors if change detected via interrupt
  if (sensortriggered) {
    sensortriggered = false;
    updateHallSensors();
  }

  // Calibrate any units that require it
  recalibrate_units();

  // Move any units pending due to drum passing origin (after they have recalibrated)
  for (uint8_t unit = 0; unit < UNITCOUNT; unit++) {
    if (splitFlap[unit]->pendingLetter > 0 && splitFlap[unit]->calibrationComplete) {
      splitFlap[unit]->moveSteppertoLetter(splitFlap[unit]->pendingLetter);
    }
  }

  // Lower priority events below
  if ((uint32_t)millis() - previousMillis >= 500) {
    previousMillis = millis();

    // Rest API server
    server.handleClient();

    //If display not moving, check if anything new to display
    if (!diplayStillMoving()) {
      displayLastStoppedMillis = millis();

      // Check if need to redisplay after reboot
      if (previous_display[0] != '\0') {
        // don't allow more than 3 reboots per period - to avoid continous running in the event of fault
        if (reboot_count++ > 3) {
          debugln(TXT_RED "HALTING due to reboot count." TXT_RST);
          while (true);
        }
        debugf("Display previous string: [%s], reboots: %d\n", previous_display, reboot_count);
        displayString(String(previous_display));
        previous_display[0] = '\0';
        getting_first_word = false;
      }

      else if (getting_first_word) {
        if (word_updates_per_hour > 0) {
          String word = wordOfTheDay();
          displayLastStoppedMillis = millis();
          debugf("Word, %02d:%02d, [%s]\n", timeinfo.tm_hour, timeinfo.tm_min, word);
          displayString(word);    
          nextWordAPIMillis = millis() + 60000; //dont check again until this minute passed
        }
        getting_first_word = false;
      }

      // Display random word according to WORDUPDATESPERHOUR
      else if (word_updates_per_hour > 0 && ((uint32_t)millis() > nextWordAPIMillis)) {
        // Only update during daytime hours
        if (getNTP(now, timeinfo)) {
          if ((timeinfo.tm_min % (60 / word_updates_per_hour) == 0) && (timeinfo.tm_hour >= 8 && timeinfo.tm_hour <= 19)) {
            reboot_count = 0;
            nextWordAPIMillis = (millis() + (3600 / word_updates_per_hour) * 1000) - 3000; //dont check again until nearly next word update time
            String word = wordOfTheDay();
            displayLastStoppedMillis = millis();
            debugf("Word, %02d:%02d, [%s]\n", timeinfo.tm_hour, timeinfo.tm_min, word);
            displayString(word);

            // For testing only (changes all characters and requires a drum rotation + calibration each time)
            // nextWordAPIMillis = (millis() + (3600 / word_updates_per_hour) * 1000) - 3000; //dont check again until nearly next word update time
            // String thisSeq = "@@@@@@@@@@@@";
            // charSeq--;
            // if (charSeq == 0) {
            //   charSeq = 39;
            // }
            // thisSeq.replace("@",String(letters[charSeq]));
            // displayString(thisSeq);

          }
        }
      }

      // Handle Button Press Code Here
      // else if (digitalRead(button1Pin) == 0) {
      //   do something;
      // }
    }
    //If display has been moving for more than 20 seconds, must be an error condition
    else if (millis() - displayLastStoppedMillis > 20000) {
      debugln(TXT_RED "Moving > 20 secs - RESTARTING!!!" TXT_RST);
      nvmem.magic = RTC_MAGIC;
      strncpy(nvmem.previous_display,save_display,13);
      nvmem.reboot_count = reboot_count;
      ESP.restart();
    }

    // Handle interactive serial commands over USB (used for debugging)
#if DEBUG == 1
    if (Serial.available()) {
      test_command = Serial.readStringUntil('\n');
      test_command.replace("\r","");
      test_command.toUpperCase();

      // if only return was pressed then repeat last command
      if (test_command.length() == 0) { 
        test_command = test_command_previous;
      }

      if (test_command.charAt(0) == char(92)) { //backslash
        print_test_menu();
      }
      else if (test_command.charAt(0) == ']') {
        test_num = test_command.substring(1,3).toInt();
        if (test_num >= 0) {
          active_menu_unit = test_num;
          debugf("Active unit set to %d\n", active_menu_unit);
        }
      }
      else if (test_command.charAt(0) == '>') {
        test_num = test_command.substring(1,5).toInt();
        if (test_num > 0) {
          debugf("Move %d flaps\n", test_num);
          splitFlap[active_menu_unit]->moveStepperbyFlap(test_num);
        }
      }
      else if (test_command.charAt(0) == '}') {
        test_num = test_command.substring(1,5).toInt();
        if (test_num > 0) {
            debugf("Move all flaps by %d\n", test_num);
            for (uint8_t unit = 0; unit < UNITCOUNT; unit++) {
              splitFlap[unit]->moveStepperbyFlap(test_num);
            }
        }
      }
      // Move stepper by a raw number of steps
      else if (test_command.charAt(0) == '~') {
        test_num = test_command.substring(1,5).toInt();
        if (test_num > 0) {
          debugf("Move %d steps\n", test_num);
          splitFlap[active_menu_unit]->moveStepperbyStep(test_num);
        }
      }
      else if (test_command.charAt(0) == '|') {
        ESP.restart();
      }
      else if (test_command.charAt(0) == '%') {
        String word = wordOfTheDay();
        debugf("Word, %02d:%02d, [%s]\n", timeinfo.tm_hour, timeinfo.tm_min, word);
        displayString(word);
      }   
      else if (test_command.charAt(0) == '+') {
        String thisSeq = "@@@@@@@@@@@@";
        // String thisSeq = "       @ ";
        charSeq--;
        if (charSeq == 0) {
          charSeq = 39;
        }
        thisSeq.replace("@",String(letters[charSeq]));
        displayString(thisSeq);
      }  
      else if (test_command.charAt(0) == '<') {
        debugln("Put ESP to sleep until power reset");
        esp_deep_sleep_start();
      }      
      else {
        test_command.toUpperCase();
        debugf("Display %s\n", test_command);
        displayString(test_command);
      }
      test_command_previous = test_command;
    }
#endif
  }

}

void print_test_menu() {
  getNTP(now, timeinfo);

  debugln(TXT_GREEN "----------------------------------");
  debugf ("     %s", asctime(&timeinfo));
  debugln("Enter a command followed by return");
  debugln("----------------------------------");
  debugln("\\   : Show this menu");
  debugln("}   : Move ALL forward number of flaps");
  debugf ("]   : Set active unit for this menu [%d]\n", active_menu_unit);
  debugln(">   : Move forward number of flaps");
  debugln("~   : Move forward number steps");
  debugln("|   : Reset Display");
  debugln("%   : Display a random word");
  debugln("+   : Test: countdown of all flaps");
  debugln("<   : Idle");
  debugln("any : display given text");
  debugln("----------------------------------" TXT_RST);
}

// Callback routine that actions the enable on or off triggered by setAutoEnable
bool setExternalPin(uint8_t pin, uint8_t value) {
  pin = pin & ~PIN_EXTERNAL_FLAG;

  // When using SLEEP instead of /ENABLE on the A4988 to save idle power, need to invert
  // debugf("mcp en pin %d set to %d\n", pin, value ^ 0x01);
  mcp_en_steppers.digitalWrite(pin, value ^ 0x01);

  return value;
}

void recalibrate_units() {
  uint8_t unitsCalibrating;
  int8_t calibrationResult;

  unitsCalibrating = 0;
  for (uint8_t unit = 0; unit < UNITCOUNT; unit++) {
    if (!splitFlap[unit]->calibrationComplete) {
      if (!splitFlap[unit]->calibrationStarted) {
        splitFlap[unit]->calibrateStart();
        unitsCalibrating++;
      }
      else {
        calibrationResult = splitFlap[unit]->calibrate();
        if (calibrationResult == 0) {
          unitsCalibrating++;
        }
        else if (calibrationResult < 0) {
          debugf("Calibration failed for unit %d\n", unit);
          debugln(TXT_RED "RESTARTING!!!" TXT_RST);
          nvmem.magic = RTC_MAGIC;
          strncpy(nvmem.previous_display,save_display,13);
          nvmem.reboot_count = reboot_count;
          ESP.restart();
        }
      }
    }
  }
}

void IRAM_ATTR sensor_ISR() {
    sensortriggered = true;
}

void updateHallSensors() {
  uint8_t newvalue;

  mcp_sensor.clearInterrupts();
  uint8_t sensor_port_current_a = mcp_sensor.readPort(MCP23017Port::A);
  uint8_t sensor_port_current_b = mcp_sensor.readPort(MCP23017Port::B);

  for (uint8_t unit = 0; unit < UNITCOUNT; unit++) {
    if (sensorPort[unit] == 'A') {
        newvalue = ((~sensor_port_current_a & sensorPortBit[unit]) == 0);
        if (!splitFlap[unit]->updateHallValue(newvalue)) {
          splitFlap[unit]->moveStepperbyFlap(1);
          splitFlap[unit]->calibrationComplete = false;
          splitFlap[unit]->calibrationStarted = false;
          splitFlap[unit]->pendingLetter = splitFlap[unit]->destinationLetter;
        }
    }
    else {
        newvalue = ((~sensor_port_current_b & sensorPortBit[unit]) == 0);
        if (!splitFlap[unit]->updateHallValue(newvalue)) {
          splitFlap[unit]->moveStepperbyFlap(1);
          splitFlap[unit]->calibrationComplete = false;
          splitFlap[unit]->calibrationStarted = false;
          splitFlap[unit]->pendingLetter = splitFlap[unit]->destinationLetter;
        }
    }
  }
}

void displayString(String display) {
  uint8_t test_length;
  char display_char;

  display.toUpperCase();
  strncpy(save_display, display.c_str(), 13); // save display in case of reboot

  test_length = display.length();
  if (test_length > UNITCOUNT) {
    test_length = UNITCOUNT;
  }
  for (uint8_t char_pos = 0; char_pos < test_length; char_pos++) {
    display_char = display.charAt(char_pos);
    splitFlap[char_pos]->moveSteppertoLetter(display_char);
  }
}

boolean diplayStillMoving () {
  boolean display_busy = true;
  display_busy = false;
  for (uint8_t unit = 0; unit < UNITCOUNT; unit++) {
    if (splitFlap[unit]->checkIfRunning()) {
      display_busy = true;
    }
  }
  return display_busy;
}

// void intToBinary(int num, char* binaryStr) {
//     for (int i = 7; i >= 0; i--) {
//         int bit = (num >> i) & 1;
//         binaryStr[7 - i] = bit + '0'; // Convert the bit to '0' or '1'
//     }
//     binaryStr[8] = '\0'; // Null-terminate the string
// }

// void debugUnitFlags(String prefix) {
//   for (uint8_t unit = 0; unit < UNITCOUNT; unit++) {
//     debugf("%s,%02d,%c,%d,%d\n", prefix, unit, (splitFlap[unit]->pendingLetter == 0) ? 95 : splitFlap[unit]->pendingLetter, splitFlap[unit]->calibrationStarted, splitFlap[unit]->calibrationComplete);
//   }
// }

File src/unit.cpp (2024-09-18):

#include "unit.h"

Unit::Unit(FastAccelStepperEngine& engine, uint8_t unit) {
  unitNum = unit;
  stepper = engine.stepperConnectToPin(unitStepPin[unitNum]);

  stepper->setEnablePin(UnitEnablePin[unitNum] | PIN_EXTERNAL_FLAG);
  stepper->setAutoEnable(true);
  stepper->setDelayToEnable(1000); // microseconds
  stepper->setDelayToDisable(2); // milliseconds
  // debugf("Unit %d Step pin set to %d\n", unitNum, unitStepPin[unitNum]);

  stepper->setSpeedInUs(rotationSpeeduS);  // the parameter is us/step
  stepper->setAcceleration(4000);

  missedSteps = 0; 
  currentLetterPosition = 0;
  destinationLetter = 0;
  pendingLetter = 0;
  calibrationStarted = false;
  calibrationComplete = false;
  currentHallValue = 1;
  lastHallUpdateTime = 0;
  }

// calc number of steps to rotate based on cumulative step error
int16_t Unit::stepsToRotate (float steps) {
    int16_t roundedStep = (int16_t)steps;
    missedSteps = missedSteps + ((float)steps - (float)roundedStep);
    if (missedSteps > 1) {
        roundedStep = roundedStep + 1;
        missedSteps--;
    }
  return roundedStep;
}

// translates char to letter position
uint8_t Unit::translateLettertoInt(char letterchar) {
  for (int i = 0; i < 45; i++) {
    if (letterchar == letters[i]) {
      return i;
    }
  }
  return 0;
}

// calc flaps to rotate to get to a specified letter
uint8_t Unit::flapsToRotateToLetter(char letterchar, boolean *recalibrate) {
    int8_t newLetterPosition;
    int8_t deltaFlapPosition;

    newLetterPosition = translateLettertoInt(letterchar);
    deltaFlapPosition = newLetterPosition - currentLetterPosition;

    if (deltaFlapPosition < 0) {
      deltaFlapPosition = 45 + deltaFlapPosition;
      *recalibrate = true;
    }
    else {
      currentLetterPosition = newLetterPosition;
    }

    return deltaFlapPosition;
}

// calc steps to rotate forward a specified number of flaps
uint16_t Unit::stepsToRotateFlaps(uint16_t flaps) {
  float preciseStep = (float)flaps * FlapStep[unitNum];
  return stepsToRotate (preciseStep);
}

// only for testing: Move stepper by a raw number of steps
void Unit::moveStepperbyStep(int16_t steps) {
    stepper->move(steps);
}

void Unit::moveStepperbyFlap(uint16_t flaps) {
    stepper->move(stepsToRotateFlaps(flaps));
}

void Unit::moveSteppertoLetter(char toLetter) {
  boolean recalibrate = false;

  destinationLetter = toLetter;

  uint8_t flapsToMove = flapsToRotateToLetter(toLetter, &recalibrate);
  debugf("Unit %02d flapsToMove %d\n", unitNum, flapsToMove);

  if (recalibrate) {
    calibrationComplete = false;
    pendingLetter = toLetter;
    debugf("Unit %02d pendingLetter '%c'\n", unitNum, pendingLetter);
    debugf("Pending,%02d,'%c'\n", unitNum, pendingLetter);
  }
  else {
    debugf("Unit %02d move to '%c'\n", unitNum, toLetter);
    moveStepperbyFlap(flapsToMove);
    pendingLetter = 0;
  }
}

// start calibration of the unit using the hall sensor
void Unit::calibrateStart() {
  calibrationComplete = false;
  calibrationStarted = true;
  calibrationStartTime = millis();

  stepper->runForward();

  // if starting within range of the sensor, need to move outside range before doing calibration
  if (currentHallValue == 0) {
      debugf("preInitialise started for Unit %d\n", unitNum);
      preInitialise = true;
  }
  else {
      preInitialise = false;
  }

  debugf("Calibration started for Unit %d\n", unitNum);
  
  stepper->runForward();
}

// continue calibration of the unit using the hall sensor
int8_t Unit::calibrate() {
  if (!calibrationComplete) {

    // If taking too long, there must be a problem
    if (millis() - calibrationStartTime > 12000) {
      currentLetterPosition = 0;
      calibrationComplete = true;
      calibrationStarted= false;
      debugf("calibration for Unit %d failed\n", unitNum);
      stepper->forceStop();
      return -1;
    }

    // if reached end of preinitialisation phase
    if (preInitialise == true && currentHallValue == 1) {
      preInitialise = false;
      debugf("preInitialise completed for Unit %d\n", unitNum);
    }
    //if still in preinitialising phase, keep moving
    else if (preInitialise == true) {
      return 0;
    }
    // if sensor reached, do calibration
    else if (currentHallValue == 0) {
      // reached marker, go to calibrated offset position
      debugf("Calb,%02d\n", unitNum);
      stepper->forceStopAndNewPosition(0);
      delay(1); // attempt to fix rare hangup
      stepper->move(calOffsetUnit[unitNum]);
      currentLetterPosition = 0;
      missedSteps = 0;
      calibrationComplete = true;
      calibrationStarted = false;
      // Reset speed
      // stepper->setSpeedInUs(rotationSpeeduS);  // the parameter is us/step
      debugf("Unit %d calibrated\n", unitNum);
      return 1;
      }

    return 0;
  }

  // just return if calibration already completed
  return 1;
}

boolean Unit::checkIfRunning() {
  return stepper->isRunning();
}

boolean Unit::updateHallValue(uint8_t updatedHallValue) {
  uint32_t timedelta;
  if (updatedHallValue != currentHallValue) {
    timedelta = millis() - lastHallUpdateTime;

    currentHallValue = updatedHallValue;
    lastHallUpdateTime = millis();
    // debugf("Unit: %d, Hall: %d, Delta: %d\n", unitNum, currentHallValue, timedelta);
    // debugf("Hall,%02d,%d,%lu,%d,%d,%d,'%c'\n", unitNum, currentHallValue, timedelta, preInitialise, calibrationStarted, calibrationComplete, pendingLetter);

    // If occasional glitch occurrs, start calibration again
    if (timedelta <= 100) {
      debugf(TXT_RED "GLITCH,%02d,%d,%d,'%c'\n" TXT_RST, unitNum, updatedHallValue, timedelta, destinationLetter);
      return false;
    }
  }

  return true;
}

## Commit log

2024-03-28 first public commit
    [Controller-PCB-BIll-of-materials.csv, PCBWay_bom.csv, PCBWay_positions.csv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]
2024-09-18 Improve recovery from error; add NETWORKNAME config
    [main.cpp, unit.cpp]
2024-10-14 prevent initial word fetch when WORDUPDATESPERHOUR set to 0
    [main.cpp]
